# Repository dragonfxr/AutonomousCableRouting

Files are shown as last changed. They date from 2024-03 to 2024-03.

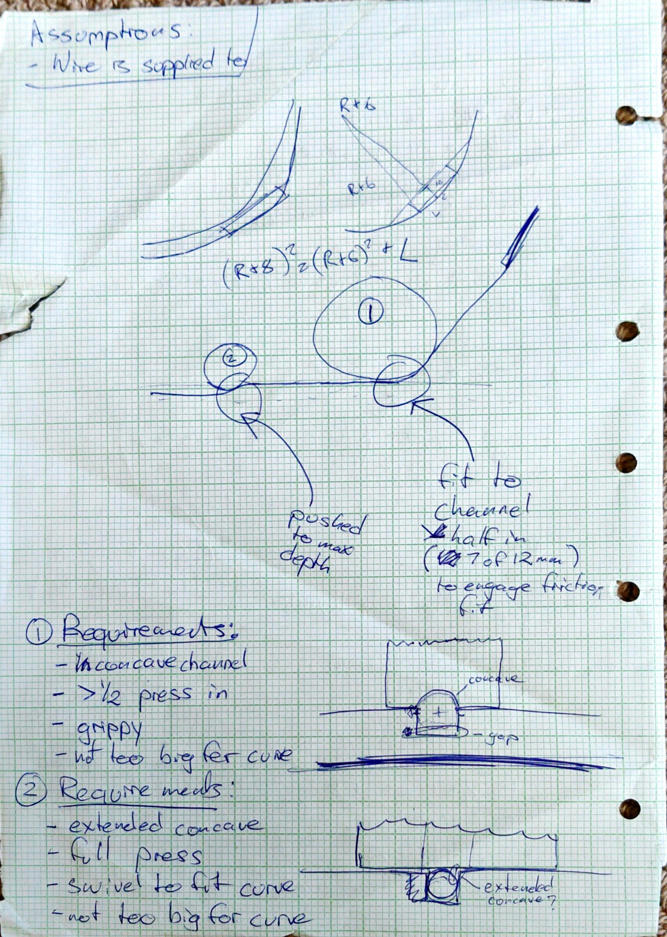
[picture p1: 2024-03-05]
Compendium/4. Routing/Design Evolution/General Sketches/2021_10_18 2_13 PM Office Lens.jpg

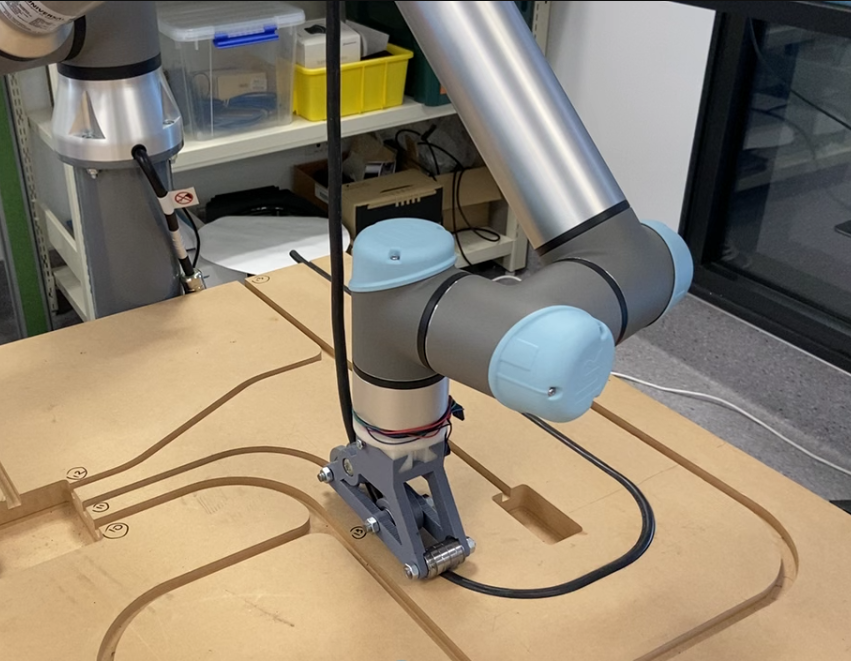
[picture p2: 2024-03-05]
Compendium/4. Routing/Final Design/Photos and Videos/process3.png

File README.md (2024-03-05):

# AutonomousCableRouting
https://www.youtube.com/watch?v=44ud-408be0

## Project Title
Research project on Autonomous Routing and Connection of Multi-Core Cables into Prefabricated Walls.

## Project Description
The demand for affordable housing is increasing rapidly. Driven by high labour costs, home
prices are climbing ever higher. Therefore, some new methods are introduced to reduce
construction costs. A solution is the automatic pre-fabrication of homes, improving construction
efficiency in terms of time and labour cost. This project focuses on automating the handling
and routing of electrical cables in pre-fabricated walls, employing a sophisticated robotic
end-effector, a path planning scheme to appropriately control the robot arm, and specially
designed connector solutions for connecting individual cable cores in 3-way junctions.

The proposed robotic end-effector is equipped with a cable feeding mechanism and it
can press-fit the electrical cables into narrow channels created in concrete pre-fabricated
walls. The end-effector shows reliable and repeatable operation. The research also presents
two types of connector designs that can facilitate the connection of the cable cores in the
junctions of pre-fabricated walls. The installation of connectors is based on a machine
vision framework implemented in MATLAB. The machine vision framework can identify
the colours of cables and locate the cables.

Robot programming and path planning relied on kinaesthetic teaching. The results showed
the speed of routing using robotic arms far exceeds manual routing.

## Acknowledgement
I would like to thank the following:

Zach Macleod, my project partner, for his passion for the project, excellent critical thinking
and professional engineering skills.

Dr Minas Liarokapis, our project supervisor, for the time and guidance throughout the
project and many suggestions are given to us.

Zuru Tech for their opinions on the project.

# How to have a look
You can always click and check the files above. If they are not obvious, please try the following:

## Video on Youtube
https://www.youtube.com/watch?v=44ud-408be0&list=PLSRmLAcBxallVHnpcKzguajrszkn9cb2G&index=4&t=2s

## Link for the research report
[Report.pdf](https://github.com/dragonfxr/AutonomousCableRouting/files/14495556/Report_xfen422.pdf)

# How to contact
If you have more advice on the project or you want to me some hints, please contact me.

Email:

russell.feng.au@gmail.com

I'm always open to feedback and collaboration. Looking forward to hearing and learning from you!

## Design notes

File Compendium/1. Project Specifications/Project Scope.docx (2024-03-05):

# Project Scope

# Research Objectives

To produce an acceptable solution for the required system, the following objectives need to be met:

- Identify what processes must be performed on an electrical cable before routing.
- Investigate what perception methods are needed to identify and localise flexible cables.
- Investigate what methods should be employed to facilitate the efficient execution of cable handling and manipulation tasks.
- Investigate what design characteristics are needed for the development of an end-effector that can manipulate flexible cables effectively.
- Examine possible cable grasping mechanisms and techniques and their capability tovary grip strength and agility.
- Examine suitable connection methods of multi-core electrical cables at 3 way junc-tions.
- Investigate what design characteristics are needed for the development of an end-effector that can install electrical connections effectively.
- Identify what methods are required to implement a routing system fully autonom-ously and ensure errors are handled correctly.
- Analyse the return on investment of the routing system compared to manual labour

# Exclusions

The following are excluded from the scope:

- Structural analysis and strengthening of parts for long life in industrial context.
  - This is because the conditions of future use are not clear, so instead the designs are used as proof of concept.
- Robot arm path planning.
  - This is because ZURU Tech has extensive knowledge and capability for path planning, further consideration would be trivial.
- Stepper motor speed control.
  - This is because motor control is already a very well-defined process, further consideration would be trivial.

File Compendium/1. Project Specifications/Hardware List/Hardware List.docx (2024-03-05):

# Hardware List

Following are the names and brief descriptions of the hardware used throughout the project:

- Prusa 3D Printers
  - A variety of Prusa 3D printer models were available for use. Used for rapid prototyping of routing end-effector models.
  - Available in the 3D printing and mechatronics labs in the 405 building at the University of Auckland. Requires training.
- Universal Robots UR5e Robot Arm
  - A mid-size robot arm which is simple to program. Used for initial testing of routing end-effector prototypes.
  - Available in the robot cell in the mechatronics lab in the 405 building at University of Auckland. Requires training.
  - Manual included.
- KUKA KR16 Robot Arm
  - A mid to large size robot arm which will be used in real-world application. Not used in this project.
  - Available in the robot cell in the mechatronics lab in the 405 building at University of Auckland. Requires training.
  - Technical specs included.
  - Serial number: 859871.
- NEMA17 Stepper Motor
  - A stepper motor for accurate and precise motor control. Used for feeding a cable for routing.
  - Available at request from technicians in the mechatronics lab in the 405 building at University of Auckland.
  - Technical specs included.
- DRV8825 Stepper Motor Driver
  - A motor driver for interfacing stepper motors to control circuits. Used for driving the NEMA17 stepper motor.
  - Available at request from technicians in the mechatronics lab in the 405 building at University of Auckland.
  - Technical specs included.
- Arduino Uno Rev3
  - A microcontroller to control stepper motor function. Used for controlling the NEMA17 stepper motor.
  - Available at request from technicians in the mechatronics lab in the 405 building at University of Auckland.
  - Schematic included.
- KINGSING KS-W1022 Multi-Core Cable and Stripping Machine
  - A stripping machine which can cut cables to length, automatically strip outer sheaths and core insulations. Used for stripping and cutting multi-core cable to the desired lengths for routing.
  - Bought by ZURU Tech for project use.
  - Manual Included.
- Sample Wall
  - A sample wall fabricated from MDF for testing of routing function.
  - Available in the mechatronics lab in the 405 building at University of Auckland or for request by engineering workshop technicians.
- Multi-Core Cables
  - Electrical cables to be routed into channels. Variety of 3-solid-core power cables and 4-stranded-core data cables.
  - Purchased by the technicians of the mechatronics lab in the 405 building at University of Auckland.
  - Specification in directory “\3. Cable Stripping Methods\Criteria”
- Consumables (by use)
  - Stepper motor circuit
    - Breadboard
    - Jumper wires
    - Capacitor
  - Routing end-effector prototypes
    - Threaded rods
    - Bolts
    - Machine screws
    - Socket screws
    - Nuts
    - Threaded inserts
    - Ball bearings
    - PLA filament
    - Elastic bands
- Workshop Tools
  - Soldering iron station
  - DC Power source
  - Multimeter
  - Manual wire stripper
  - Side cutters
  - Drill
  - Mallet
  - Hacksaw
  - Files
  - Screwdrivers
  - Allen keys
  - Spenners
  - Pliers
  - Vernier caliper
  - Utility knife
  - Scraper
  - PPE

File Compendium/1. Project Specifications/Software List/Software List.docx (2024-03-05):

# Software List

Following are the names and brief descriptions of the software used throughout the project:

- Google Drive
  - The shared file storage system was essential for accessibility and collaboration. Functionality for document creation was also used for presentation preparation, note taking and brainstorming.
  - Free online service - accessed through university Google accounts.
- Microsoft Office Suite
  - The Word and Powerpoint applications were useful for report writing and slideshow presentations respectively. They generally create a slightly more refined finish than Google Drive.
  - Licensed through the University of Auckland - free for students.
- Overleaf
  - Useful tool for creating an organised and polished final report. Outputs a professional looking document.
  - Licensed online software through the University of Auckland - free for students.
- Autodesk Inventor Professional 2019/2021
  - 3D CAD modelling software for creating designs, printable parts and renders.
  - Licensed through the University of Auckland - free for students.
- PrusaSlicer
  - Open-source slicing software for generating a 3D printable G-code file from a stl CAD file. Designed specifically for Prusa 3D printers which are used heavily by the University of Auckland.
  - Free through the University of Auckland - free for students.
- MATLAB
  - Versatile high-level programming language. Used for function calculations and image processing scripts.
  - Licensed through the University of Auckland - free for students.
- Arduino IDE
  - Open-source programming software designed to be compatible with an Arduino microcontroller. Used for stepper motor control.
  - Free downloadable software.
- Fritzing
  - Electronics circuit and PCB design software. Used for design of stepper motor control circuit.
  - Paid downloadable software.
- UR5e Robot Arm Controller
  - Built-in controller software for programming movement of a UR5e robot arm. Used for testing of routing end-effectors by moving by a manually defined path.
  - Available for use at the University of Auckland
  - Manual included in directory “\1. Project Specifications\Hardware List”

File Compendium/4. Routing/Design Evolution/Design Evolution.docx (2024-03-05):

# Design Evolution

# Prototype 1: Hand-held Roller

Designed as an initial test for rolling a cable into the sample wall. Was designed to be spring loaded and hand-held. For 10mm stranded cable. CAD models were deleted.

Design was abandoned in favour of a robot-mounted one.

## Advantages:

- Concave wheel profile

## Issues:

- Requires large downwards force
- Requires many elastic bands
- Prone to slipping
- Difficulty with corners

# Prototype 2: Crank Feeder

Designed for no contact to the sample wall, just to feed the cable with enough force to press-fit. Hand-cranked for 10mm stranded cable. CAD models were deleted.

Design was abandoned.

## Advantages:

- Concave wheel profile
- No contact/wear with wall

## Issues:

- Requires large grip force
- Prone to slipping
- Push-fit depth is unpredictable
- Prone to cable raising after routing
- Design tolerances were too big
- Hand cranked

# Prototype 3: Framed Roller Initial

Designed for robust routing and lowered variability. A series of wheels would align then press the cable into the channel. For 12mm solid cable.

## Advantages:

- Concave wheel profile
- Robust routing method

## Issues:

- Hole-edge distance too small
- Structure is too thin and flimsy
- Not enough holes for arm mounting
- Feeding hole didn’t work
- No stepper

# Prototype 4: Framed Roller Iteration 1

Iteration of previous prototype. For 12mm solid cable. Some CAD files altered and no renders.

## Advantages:

- Concave wheel profile
- Robust routing method
- Increased thickness of structure (including hole-edge distance)
- Better arm mounting holes
- Replaced feeding hole with roller

## Issues:

- No Stepper
- Arm mounting holes don’t fit screws

# Prototype 5: Framed Roller Iteration 2

Iteration of previous prototype. For 10mm stranded cable for better performance. All CAD files altered and no renders.

## Advantages:

- Concave wheel profile
- Robust routing method
- Increased thickness of structure (including hole-edge distance)
- Replaced feeding roller with a stepper motor driven feeding mechanism

## Issues:

- Loaded feed wheel doesn’t close enough
- Stepper mount screws stick out too much
- Stepper mount screws are incorrectly positioned
- Arm mounting holes don’t fit screws
- Driven wheel isn’t supported opposite stepper properly - screw doesn’t thread into anything
- Feed wheels sometime slip

# Prototype 6: Framed Roller Final Iteration

Iteration of previous prototype. For 10mm stranded cable.

## Advantages:

- Concave wheel profile
- Robust routing method
- Increased thickness of structure (including hole-edge distance)
- Replaced feeding roller with a stepper motor driven feeding mechanism
- Increased movement on loaded wheel
- Bored and rearranged stepper mount screws
- Changed arm mounting to dovetail mount with extra piece
- Inserted screw “key” opposite stepper on driven wheel

## Issues:

- Feed wheels sometime slip
- Does not accommodate different cable sizes
- Stepper motor struggles (might just be making lots of noise)

# General Sketches

Workbook sketches which detail previous designs and iterations.

# Stepper Motor

Contains:

- Fritzing circuit diagram for the stepper motor
- Figure of circuit diagram
- Basic stepper motor control script
- Stepper motor circuit description

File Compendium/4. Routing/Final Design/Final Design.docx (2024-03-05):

# Final Design

# Description

Read the end of year reports in “\9. Deliverables” to read a description of the final end-effector design.

# Process

- A cable to be routed is gripped between the driven and loaded wheels as the spin.
- The cable is then fed to the aligning wheel which will place the cable into the channel and half press-fit it.
- The push roller will then roll over the half pressed cable and fully press-fit it into the channel.

# Connection to Robot Arm

A dovetail shaped mount is bolted onto either the KR16 or UR5e robot arm. Then the frame of the end-effector is slid on the dovetail and bolted with a through-hole.

# Issues:

- Feed wheels sometime slip
- Does not accommodate different cable sizes
- Stepper motor struggles (might just be making lots of noise)

# Results:

Successfully routed 11 out of 12 initial runs with a 10mm stranded core cable. The failure mode was only slight lifting of the cable, but not removal from the channel.

Routes path in 16s.

Can also route 12mm solid core cables, however, no records were taken from this.

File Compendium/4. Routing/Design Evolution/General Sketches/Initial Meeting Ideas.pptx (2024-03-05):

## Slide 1

Russell and Zach
Conceptual designs combined together to create a working whole - or separated for use in different solution

Potential solution for groove-alignment, adhesive-
extrusion & rolling-cable-layer

Side view:

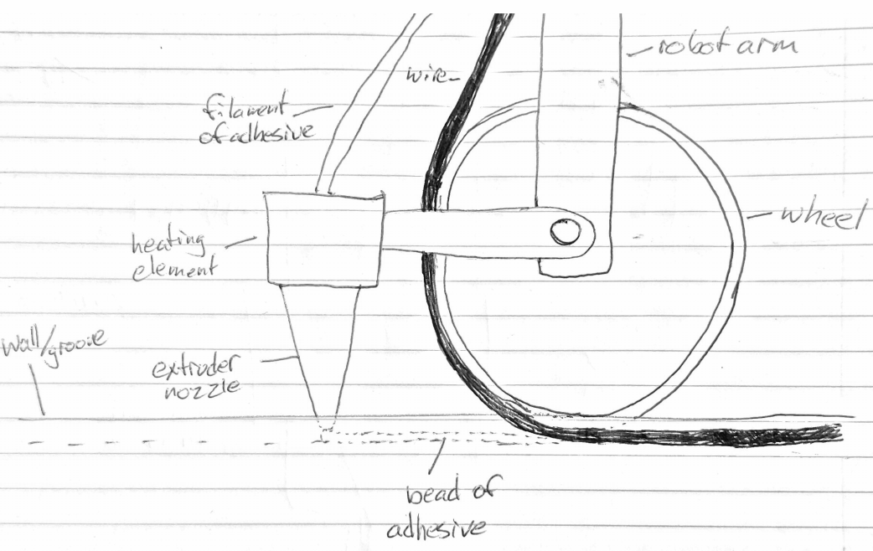
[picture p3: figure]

Potential Process:
Use a separator to separate each core by wire stripping with a moveable blade

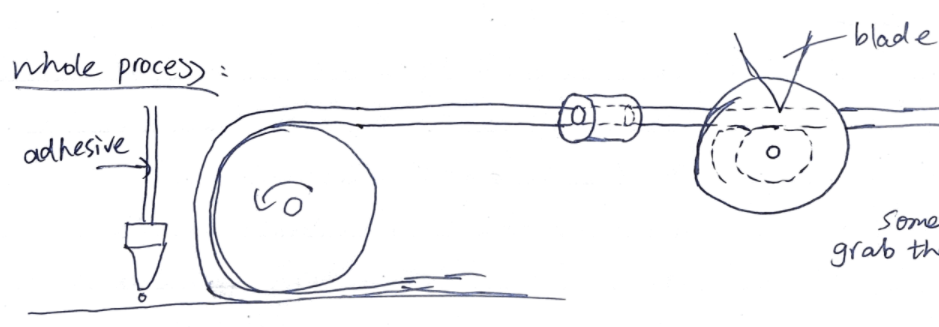
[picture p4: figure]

Potential Process: Repeated use of static mounted wire-stripping tool

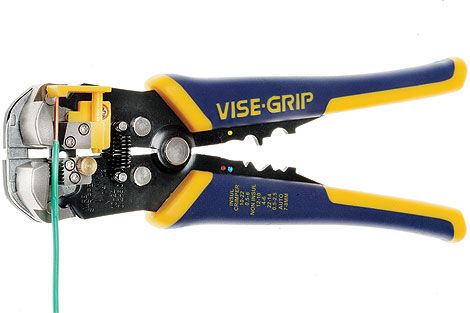
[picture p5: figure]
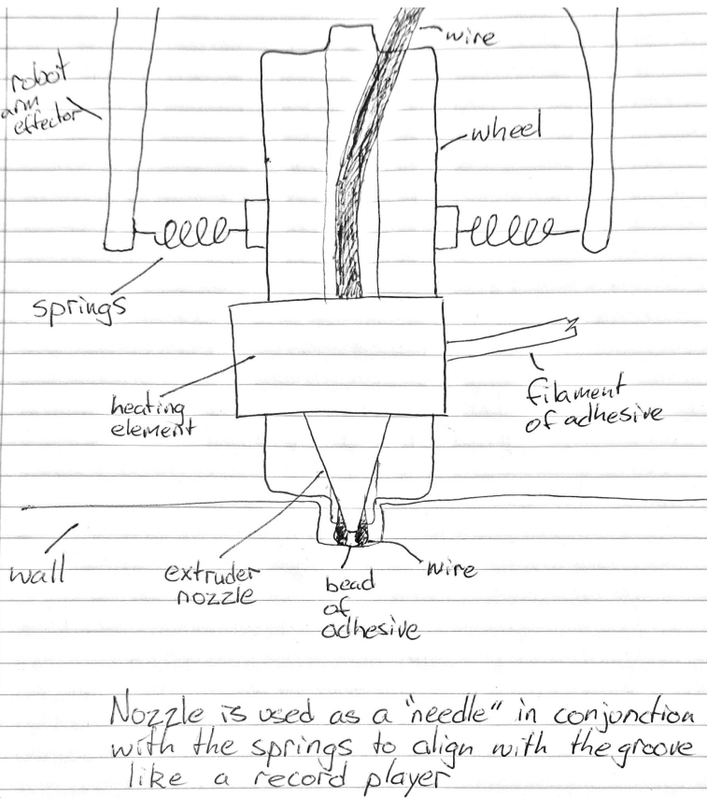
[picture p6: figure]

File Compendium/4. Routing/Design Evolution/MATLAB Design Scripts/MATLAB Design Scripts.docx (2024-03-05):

# MATLAB Design Scripts

1. MaxAlignWheelRadius

Finds the max radius of the drive wheel considering the radius of the cable to be layed, the min depth that the cable is to be pushed in (from middle of the cable) and the min ratio of the total cable press force which is pushing the cable down.

Discarded from prototype 4 because the aligning wheel no longer fits into the channel.

2. PushRollerBearingCount

Finds the number of bearings needed for the push roller considering the radius of the cable to be layed, the horizontal distance between the two axles, and the width of the bearings.

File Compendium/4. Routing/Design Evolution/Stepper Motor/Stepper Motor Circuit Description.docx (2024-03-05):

# Stepper Motor Circuit Description

The stepper motor circuit contains:

- NEMA17 stepper motor
- Jumper wires
- Basic breadboard
- 100 microfarad capacitor - for reducing voltage spikes on connection
- DRV8825 stepper driver
- Arduino Uno Rev3 microcontroller
- Power source - found to work well at 20V

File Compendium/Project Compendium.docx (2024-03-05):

Compendium Structure

The project compendium provides all materials needed for the project

1. Project Specifications
- Zuru Tech Materials
- Hardware List
- Software List
- Project Scope
2. Related work
3. Cable Stripping Method
4. Routing
- Final Design
- Design Evolution
5. Connector
- Insulation Piercing Connectors
- Insulation Displacement Connectors
- Initial Sketches
6. Image Processing
- MATLAB Script and Sample Images
- Indicative Progress Images
7. Future Work
8. Meeting Minutes and Slides

What is in each folder:

Project Specifications

The hardware and software required for the project, including manual and specification sheets for equipment.

Related work

The existing research related to the project. All research documents are categorized according to topics.

Cable Stripping Method

The cable stripping method selection criteria and video and photo of the selected stripping machine.

Routing

This folder contains the design evolution of the end-effector, including four prototypes, MATLAB scripts used in design and the stepper motor design. The CAD model, videos and photos for the final design is also in this folder, including the routing process and cable feeding using stepper motor.

Connectors

The CAD models and renders of two types of connectors as well as the initial brainstorming sketches.

Image Processing

This folder contains the MATLAB script used for image processing, sample Images and indicative progress images.

Future Work

A document describes the potential further development.

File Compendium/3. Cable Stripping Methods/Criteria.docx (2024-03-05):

# Criteria

# Cable Specifications

All cores are covered in coloured PVC insulation and a separate black outer PVC sheath.

Identification No. | No. of Cores | Cross-Sectional Area (mm²) | Core Type | Usage
1 | 3 | 2.5 | Solid | Power
2 | 3 | 4 | Solid | Power
3 | 3 | 6 | Solid | Power
4 | 4 | 1.5 | Stranded | Data
5 | 4 | 2.5 | Stranded | Data

# Cable Stripping Methods Comparison

Stripping Method | Advantages | Disadvantages
Laser | - Fast - Experiences no wear - Insulation vaporised | - Manual removal is required - Expensive
Chemical | - Cheap | - Not fit for purpose (magnet wires only) - Slow - Not environmentally friendly
Mechanical (chosen) | - Suitable for multi-core cable cutting. - Automatic removal | - Need to purchase from China
Abrasive | - Fast | - Leftover insulation dust - single-core cables only

# Alternative Methods

The following stripping methods were excluded from comparison because they were clearly not fit for purpose:

- Ultrasonic
  - Very uncommon
- None
  - Infeasible for accurate connection

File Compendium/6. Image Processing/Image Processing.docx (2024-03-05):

# Image Processing

The image processing takes images of the cables after they have been routed. Then the MATLAB script is given images which are cropped from the taken photo. The script gives the order of insulation colours of the cores so that they can be correctly connected.

For more information on the MATLAB script, read the description in the file. For more information on the process, read the final reports in “\9. Deliverables".

# Assumptions

- Unchanging light and camera conditions so that colours are not subject to much variation in images.
  - Achieved by mounting an LED on the connector end-effector.
- The images can be taken from the same place relative to the junction each time so that the script knows where to identify the insulation could patterns every time.
  - Achieved by mounting the camera on the connector end-effector and path planning for this process.

# Indicative Process Images

1. Shows the working line of the script.
2. Shows only the pixels identified as one of the insulation colours, as well as the working line.
3. Shows the average rows for each insulation colour, as well as the workling line.

# Results

100% accuracy with the sample images. The differing light conditions require the range of brown to be altered.

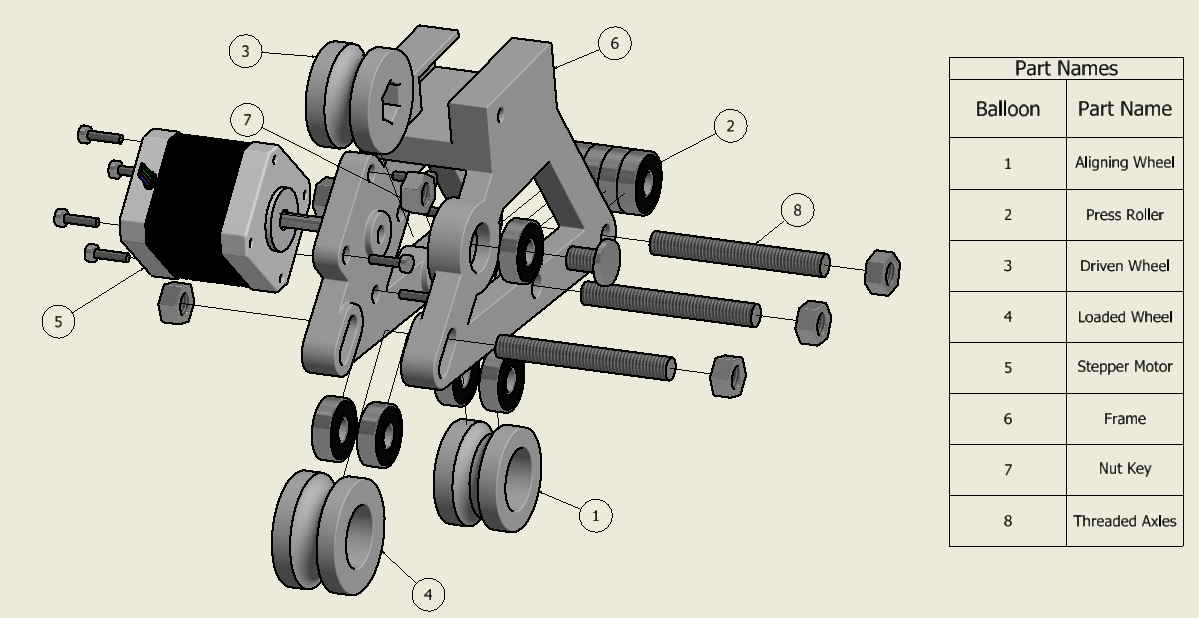
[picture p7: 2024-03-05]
Compendium/4. Routing/Final Design/CAD and Renders/Exploded.PNG

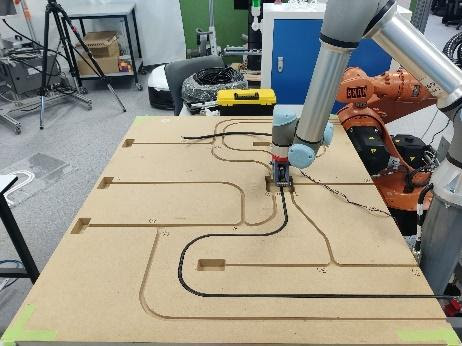
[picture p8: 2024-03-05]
Compendium/4. Routing/Final Design/Photos and Videos/timeseries6.jpg

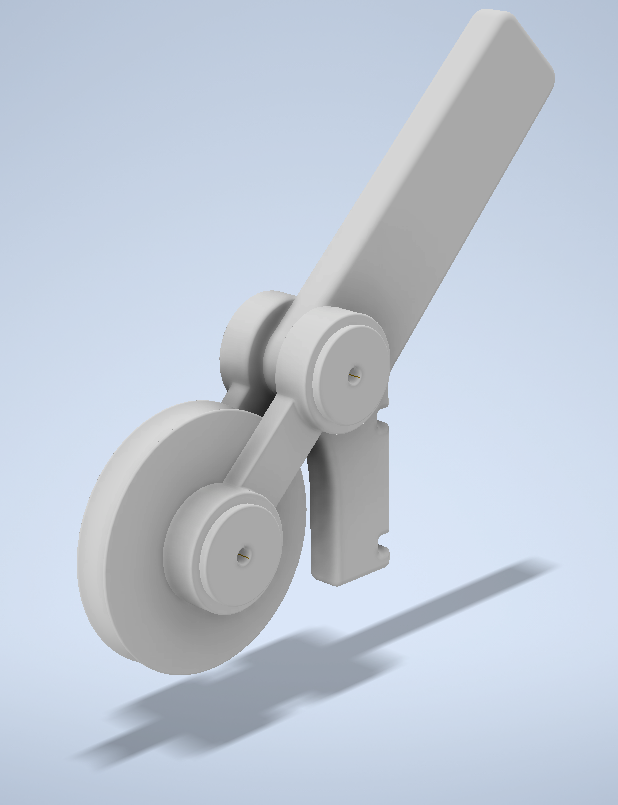
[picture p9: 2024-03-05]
Compendium/4. Routing/Design Evolution/Prototype 1_ Hand-held Roller/Prototype 1 Render.PNG

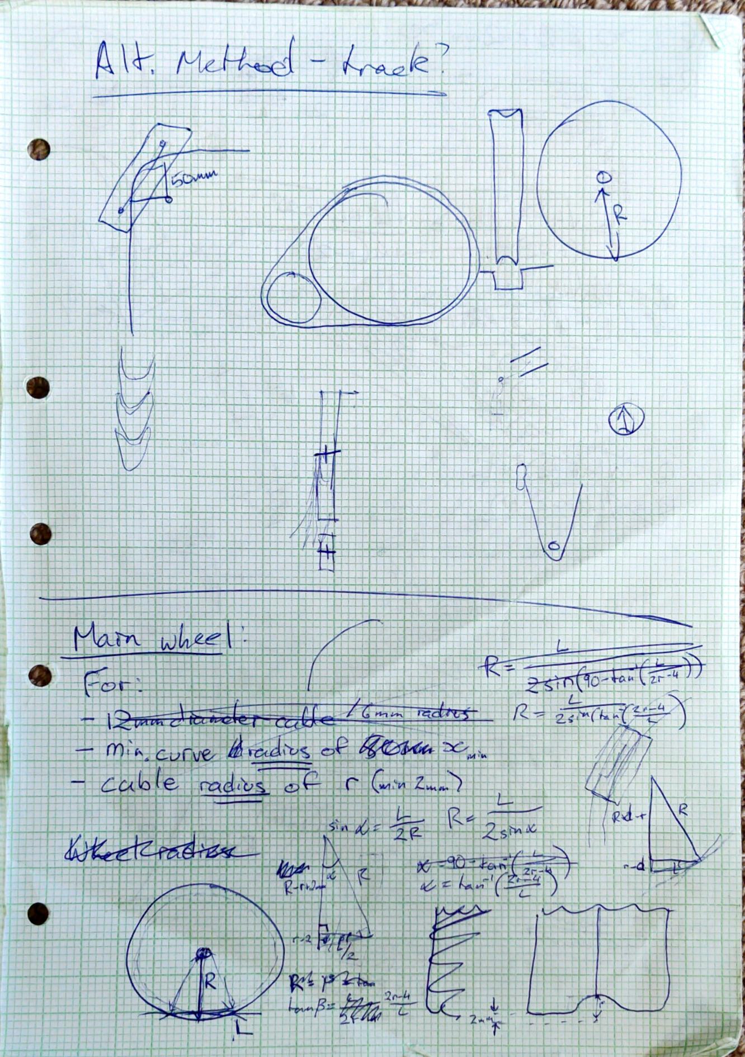
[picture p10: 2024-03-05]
Compendium/4. Routing/Design Evolution/General Sketches/2021_10_18 2_14 PM Office Lens.jpg

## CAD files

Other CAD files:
Compendium/4. Routing/Final Design/CAD and Renders/Assembly.dwg
Compendium/4. Routing/Design Evolution/Prototype 3_ Framed Roller Initial/KukaHead.0012.ipt
Compendium/4. Routing/Design Evolution/Prototype 4_ Framed Roller Iteration 1/AlignWheelHalf_12mm.ipt
Compendium/4. Routing/Design Evolution/Prototype 4_ Framed Roller Iteration 1/Assembly_NoStepper.iam
Compendium/4. Routing/Design Evolution/Prototype 4_ Framed Roller Iteration 1/Frame_12mm_nostepper.ipt
Compendium/4. Routing/Design Evolution/Prototype 4_ Framed Roller Iteration 1/LeadWheel_12mm.ipt
Compendium/4. Routing/Final Design/CAD and Renders/AlignWheelHalf_10mm.ipt
Compendium/4. Routing/Final Design/CAD and Renders/Assembly.iam
Compendium/4. Routing/Final Design/CAD and Renders/Assembly.ipn
Compendium/4. Routing/Final Design/CAD and Renders/Bearing.ipt
Compendium/4. Routing/Final Design/CAD and Renders/DriveWheel_10mm.ipt
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

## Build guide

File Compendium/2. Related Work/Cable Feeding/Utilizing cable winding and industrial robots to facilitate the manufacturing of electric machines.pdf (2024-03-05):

## Utilizing cable winding and industrial robots to facilitate the manufacturing of electric machines

## Erik Hultman n , Mats Leijon

Division for Electricity, Uppsala University, Box 534, 751 21 Uppsala, Sweden

article info

Article history:
Received 18 November 2011
Received in revised form
5 June 2012
Accepted 25 June 2012
Available online 24 July 2012

Keywords:
Stator winding
Automated production
Industrial robot
Electric machine assembly
Powerformer
Wave energy converter

abstract

Cable wound electric machines are used mainly for high voltage and direct-drive applications. They can be found in areas such as wind power, hydropower, wave power and high-voltage motors. Compared to conventional winding techniques, cable winding includes fewer manufacturing steps and is therefore likely to be better suited for automated production. Automation of the cable winding production step is a crucial task in order to lower the manufacturing costs of these machines. This article presents a production method using industrial robots for automation of cable winding of electric machine stators. The concept presented is validated through computer simulations and full-scale winding experiments, including a constructed robot-held cable feeder tool prototype. A cable wound linear stator section of an Uppsala University Wave Energy Converter and its winding process is used as a reference in this article. From this example, it is shown that considerable production cycle time and manufacturing cost savings can be anticipated compared to manual winding. The suggested automation method is very flexible. It can be used for the production of cable wound stators with different shapes and sizes, for different cable dimensions and with different winding patterns.
& 2012 Elsevier Ltd.
1. Introduction

Fully automated manufacturing of conventional electric machines, both motors and generators, is well known today and has been globally introduced in factories for a few decades [1–5]. It has been widely recognized that automated production lines are necessary to survive in today’s global electric machine market [6–8]. Designing with production in mind has been an important key in the process towards automation of electric machine manufacturing [2,5,9].
One of the most challenging operations to automate in electric machine manufacturing is the winding of the stator. For conventional machines using coils of inductor wire or rectangular inductor bars, different automated winding methods have been developed. A less common electric generator design, known as the Powerformer, utilizes cables for the stator winding. This concept has some important advantages, including reduced system losses and fewer winding production steps [10–15]. However, no published fully developed automated cable winding production method has been found.
Advances in the industrial robot technology during the last years have enabled robotized automation of advanced tasks that could only be done manually before, some with similarities to winding technology. They also allowed increased production volumes and flexibility for already existing automated production lines [16–22]. A driving actor in this is the automobile industry, with large investments in fully robotized automated production lines along with research and development of new robot applications for manufacturing [23–25]. Industrial robots often introduce more flexible automation solutions, due to their large workspace and programming possibilities, compared to methods based on task-specific, stiff automation machines. This flexibility is very suitable for the production of electric machines since rapid changes in production due to small and often varying product series are common. Thus robots are sometimes used for stator winding operations [7,26].
A specific cable winding process, the stator winding of a direct-driven linear permanent magnet cable wound generator stator section used in an UU WEC,¹ will be used in this article to exemplify a full-scale cable winding production step.
The aim of the work presented in this article is to suggest and validate a production method to facilitate electric machine manufacturing by using industrial robots to automate cable winding in electric machine stators. Even though the generator example presented here is a linear generator used in a WEC, the presented method should be applicable for other cable wound electric machines as well, including the more common rotating machines.

Contents lists available at SciVerse ScienceDirect

journal homepage: www.elsevier.com/locate/rcim

# Robotics and Computer-Integrated Manufacturing

0736-5845 & 2012 Elsevier Ltd.
http://dx.doi.org/10.1016/j.rcim.2012.06.005

n Corresponding author. Tel.: þ46 18 471 34 96; fax: þ46 18 471 58 10.
E-mail address: erik.hultman@angstrom.uu.se (E. Hultman). | 1 Uppsala University Wave Energy Converter.

Robotics and Computer-Integrated Manufacturing 29 (2013) 246–256

Open access under CC BY-NC-ND license. (http://creativecommons.org/licenses/by-nc-nd/3.0/)

Open access under CC BY-NC-ND license. (http://creativecommons.org/licenses/by-nc-nd/3.0/)

2. Method

The development of an industrial robot production cell is a complex task with many different steps. Some key methods used in this work have been: the choice of an appropriate robot model, the design of equipment in a 3D-CAD environment, offline robot cell programming and experiments, the construction of a cable feeder tool prototype and full-scale winding experiments. The main process chain is explained in Fig. 1.
Since this is an iterative process where the cell and tool design, robot programming and winding process are adjusted to each other numerous times before a satisfying solution is found, the results in Sections 4–6 only present the final versions of the automation method, the robot cell layout, the cable feeder design and the robot cell simulations.
2.1. Computer simulations of the robot cell

Offline robot programming can be an important key in evaluating and designing a new robot cell, before building a full scale cell. In this paper, ABB RobotStudio [27] is used for offline robot simulations. With this computer software, appropriate industrial robot models and number of robots regarding reach and positioning can be investigated. Also, the reach of the robots over the work object can be optimized with different tool designs. As the robot models, tool design and cell design are decided, the full robot programming can be tested with the simulation cell, including simulating sensors. However, even though offline software can save expensive robot and production time, some special events and physical states, including deformable objects, might be hard to fully simulate. Thus offline simulations must often be followed by full scale physical robot cell experiments.

2.2. Economical calculations

A new automated robot cell should be economically evaluated and compared to present and alternative production methods. One important figure, used to determine the value of the investment, is the net present value, which is calculated using Eq. (1) where NPV is the net present value, n is the economical lifetime of the investment, Ct is the net cash flow at time t and i is the discount rate. Another useful figure is the payback period, which is calculated by solving Eq. (2) where T is the payback period. NPV ¼ Xn

t ¼ 0

Ct
ð1þiÞ
t | ð1Þ

XT

t ¼ 0

Ct ¼ 0 | ð2Þ
3. Automated cable winding

This section presents some necessary background theory in developing an automated cable winding production cell, including existing stator winding techniques, the Powerformer concept, the WEC stator winding example used in this work, the most important design requirements and the basic conceptual choices used as a starting point for this automation.

3.1. Stator winding schemes

An electric machine can either be a motor, converting electric energy to mechanical energy, or a generator, converting mechanical energy to electric energy. The two main parts of an electric machine are a rotating rotor and a stationary stator. For linear machines, a linearly moving translator replaces the rotor. The basic process of the electromechanical energy conversion can be demonstrated by moving a magnet in and out of a closed conductor loop. The mechanical energy moving the magnet converts to electric energy, inducing a voltage and a current starts to flow in the conductor. This represents a linear generator design where the magnet illustrates the translator part and the conductor loop illustrates the stator. In an electrical machine the conductor loop is usually mounted inside slots in the stator and is referred to as the stator winding.
The ratio of the in-slot winding cross section area to the total available slot area, referred to as the slot fill-factor, is often used to describe stator windings. For a given stator design, the slot fill-factor represents the level of material utilization in the machine and therefore it is desired to have this ratio as high as possible. However, the slot fill-factor cannot be used by itself when comparing different stator designs since other aspects often influence the overall machine performance more.
Conventional electric machines mainly use strands of inductor wire or rectangular inductor bars for the stator winding, see Figs. 2 and 3. Using the inductor wire strand design, the coils can either be wound directly in the stator slots using special tools or be prepared outside the stator and then inserted into the stator slots. In-slot winding eliminates the extra production step of inserting the coils into the stator. On the other hand this method is not able to create windings with as high a slot fill-factor as outside winding, since the winding tool requires some space inside the slot and there is a minimum distance required between the stator teeth in order for the winding tool to be able to reach inside the slots [28].

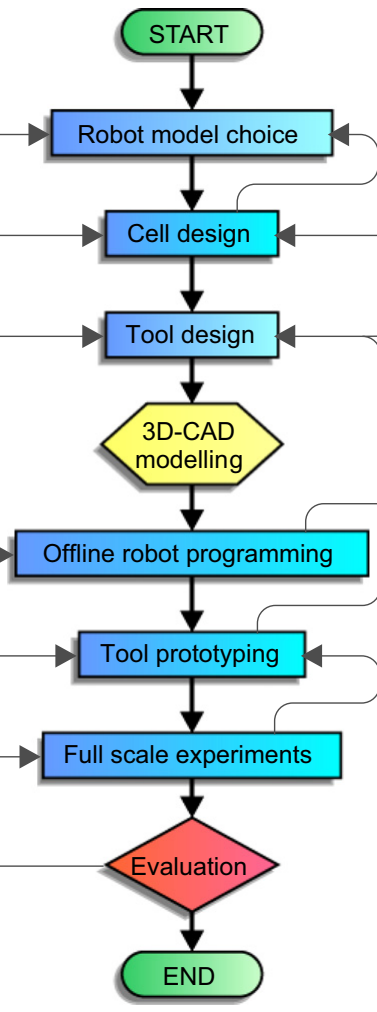
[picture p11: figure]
START; Robot model choice; Cell design; Tool design; 3D-CAD modelling; Offline robot programming; Tool prototyping; Full scale experiments; Evaluation; END

Fig. 1. Method used in the work described in this article.

E. Hultman, M. Leijon / Robotics and Computer-Integrated Manufacturing 29 (2013) 246–256 | 247

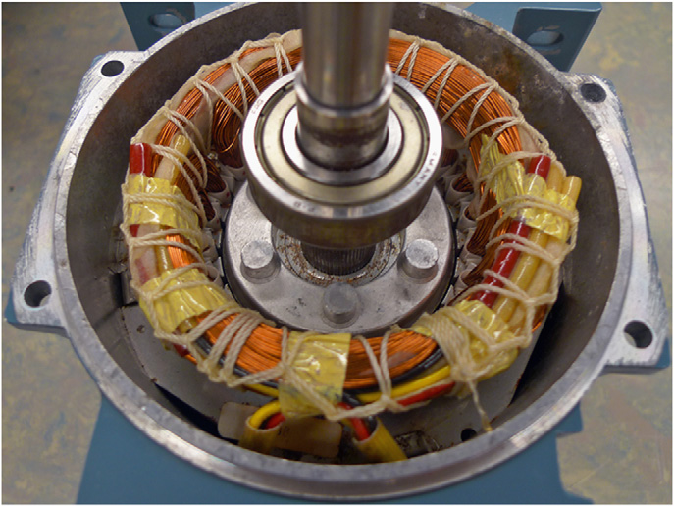
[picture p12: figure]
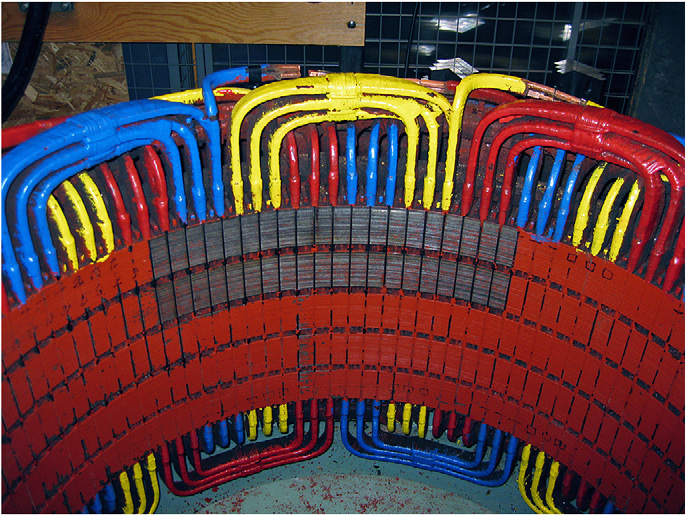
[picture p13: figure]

Preparing the windings outside the stator enables better packed and larger windings with a higher slot fill-factor, but the windings must be inserted into the slots and the stator design must be adjusted for this [9]. An alternative method is to split the stator in toothsegments and wind each segment separately [29–32]. As a result, a higher slot fill-factor can be accomplished, but an extra assembly production step for the stator is introduced. Other research suggests a sectional stator design that allows the stator slots to be opened to facilitate the winding and improve the slot fill-factor [33]. When it comes to larger machines, mostly generators, rectangular inductor bars are often used for the stator winding. Automation for insulating and forming these bars is available but the insertion is mostly done by hand due to the small production series and the large generator size [3]. Automated winding techniques for other generator designs exist too [34]. Insulation of the windings, winding fixation and end windings connection are important production steps for all conventional electric machine stators.

3.2. Cable wound machines

Cable wound generators, a concept known as the Powerformer or Very High Voltage machines, have some important advantages compared to conventional generators. Using high voltage power cables in the stator winding, a Powerformer generator allows generation of electricity at grid transmission voltage levels, thus eliminating the need for a step-up transformer between the generator and the grid. Among the benefits with this technique are reduced system losses, better network stability, smaller investment costs and less overall environmental impact [10–15]. Another important advantage of cable wound electric machine stators is that the number of manufacturing assembly steps for the stator winding are reduced. Using power cables in the winding eliminates the production steps of insulating the windings during the stator assembling, possible insertion of pre-wound coils into the stator slots and securing the windings in the stator slots, while the need for end windings connection is reduced. The full cable winding process is performed by feeding the power cables back and forth through the stator slots, from the top and bottom of the stator. Since cable wound generators and motors are still much less common than their competitors and because only small series with large machines based on this technique have been manufactured today, there is as yet no method developed for fully automated cable winding of electric machines. Manually assisted cable winding of large-scale generators are these days performed with the help of several cable feeder tools [35].

3.3. The UU WEC stator cable winding example

The specific cable winding example considered in this article is the stator winding of a direct-driven linear cable wound generator used in a WEC unit prototype constructed within the Lysekil project at The Swedish Centre for Renewable Electric Energy Conversion at Uppsala University. This technology is described in more detail in [36,37]. Fig. 4 shows the UU WEC generator design, Fig. 5 shows a cable wound UU WEC stator section that is mounted inside an UU WEC. The stator section is about 2 m long, about 0.5 m wide and is divided in the middle by a 30¹ angle. The slot hole diameter, through which the winding cable is fed, is 8 mm and the average outer diameter of the winding cable is 7.2 mm. A three-phase wave winding pattern with some modifications is used. This article will however assume and focus on a pure three-phase wave winding, see Fig. 6, since this is an obvious starting point even for other winding patterns.
A condition for this WEC technique to be competitive on a global market is that the production cost is low. The technique is intended for future large series production, which makes the manufacturing suitable for automation. Automated cable winding has an important role in this process.

Fig. 3. A stator winding with copper bars, in a hydropower generator.

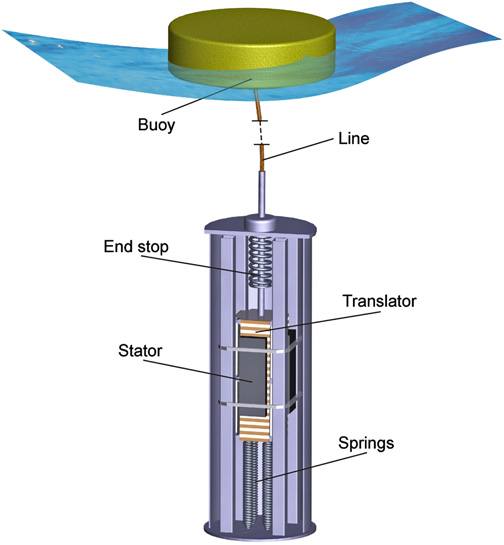
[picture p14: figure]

Fig. 4. The UU WEC unit design.

Fig. 2. A stator winding with strands of induction wire, in a small electric motor.

248 | E. Hultman, M. Leijon / Robotics and Computer-Integrated Manufacturing 29 (2013) 246–256

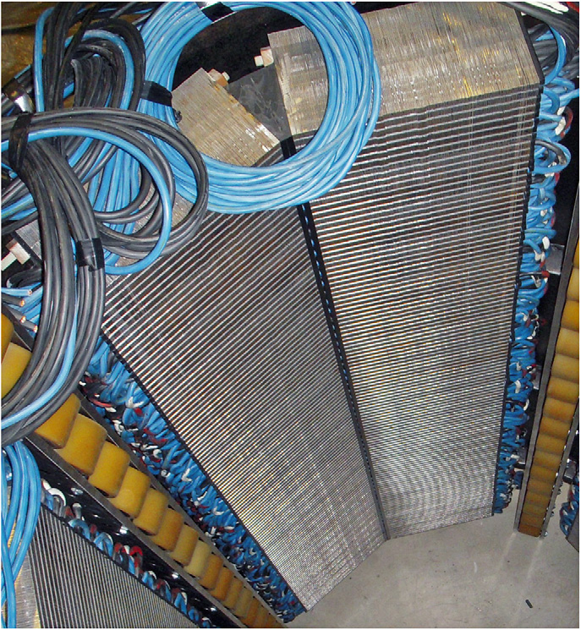
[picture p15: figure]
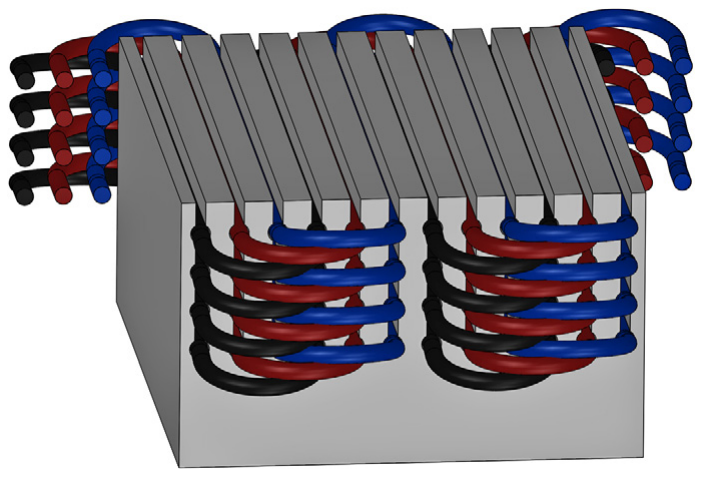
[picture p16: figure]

3.4. Requirements of automated cable winding

In developing an automation method for cable winding, some important general cable winding issues, presented in this subsection, must be considered.
As can be understood from the UU WEC stator example in Figs. 5 and 6, a cable must be fed from the sides of the stator slot by slot, so insertion of a complete winding from above is not possible. Numerous cables are instead fed back and forth through the whole stator in a specific winding pattern. The cables are then connected to each other at the end of the windings. A high stator slot fill-factor is desired; therefore the cables must be fitted tightly into the slots. The cable must be handled with care to avoid being damaged due to for example a too small bending radius, buckling or wear. Enough high cable feeding forces must be guaranteed so that the cable does not get stuck inside the stator during winding. The fed length of the cable must be controlled in order to get short end windings on the stator sides. During the winding process, earlier created end windings must sometimes be pushed down to prevent them from covering unwound slot holes and disturb the winding process. Some further general requirements of the automation are that the layout of the automation should be suitable for direct implementation in a factory production line, the need for human interaction in the production is kept to a minimum and the automation method is as simple and robust as possible. Moreover, high flexibility is needed to enable adjustments to production of different machines and the winding production cycle time and investment cost must be low.
Regarding flexibility, there are a few aspects to keep in mind. To begin with, it is important that the final automation method can be adjusted for different cable dimensions and different winding patterns. Equally important is that both linear and circular stators of different sizes can be wound with the same production technique.
4. Suggested developed automation solution

In this section the suggested developed automation solution for cable winding is presented together with the design and the constructed prototype of an essential winding tool used in this solution.

4.1. Basic conceptual automation method choices

None of the existing stator winding automation techniques for conventional machines described in Section 3.1 can be implemented for cable wound machines, mainly because the existing techniques are not able to deal with cables and feed them through the stator. Therefore another winding method is required. The work presented in this article will focus on the conceptual cable winding method described in [38], since this concept has the potential to deal with the requirements presented in Section 3.4. To push and pull a cable through the stator during winding, a cable feeder must be used. Preferably one cable feeder is used on each side of the stator so that the cable end can always be caught when being pushed through from the opposite side. Some of the demands on this cable feeder are that it must be capable to create and transfer a high enough feeding force to the cable, it must be able to catch, hold and let go of the cable, it must be able to direct the cable straight into the stator slots, it must not damage the cable, it must be possible to position it close to the stator sides without colliding with completed end windings and it should have the capability to push down end windings blocking a stator slot. Further, it should be possible to position the cable feeder against the stator sides with high accuracy, so that it can feed the cable straight into a slot and catch a cable coming out from a slot. A final requirement on the cable feeder is that it must be fairly easy to adjust within reasonable limits to different cable dimensions, stator sizes, stator shapes and winding patterns.
There are some cable feeders on the market today, but they are mostly designed to be used with large diameter cables. Consequently, these tools are often space consuming and lack options such as cable steering and the possibility to easily open up fully, which are essential for automated cable winding. No ideal feeder that can fulfill the requirements mentioned above has been found. Therefore a new cable feeder has been designed by developing an automated winding cell.
Since the cable cannot be fed through all the stator slots at the same time, a cable parking with temporary cable storages is needed. In addition, a cable supply from where new cable can be collected is needed together with equipment to prepare the cable

Fig. 6. Pure three phase wave winding pattern used as reference in this article. Note that this illustration is simplified compared to the UU WEC stator, for example there are eight slot holes per slot in the UU WEC stator.

Fig. 5. A cable wound UU WEC stator section mounted inside an UU WEC.

E. Hultman, M. Leijon / Robotics and Computer-Integrated Manufacturing 29 (2013) 246–256 | 249

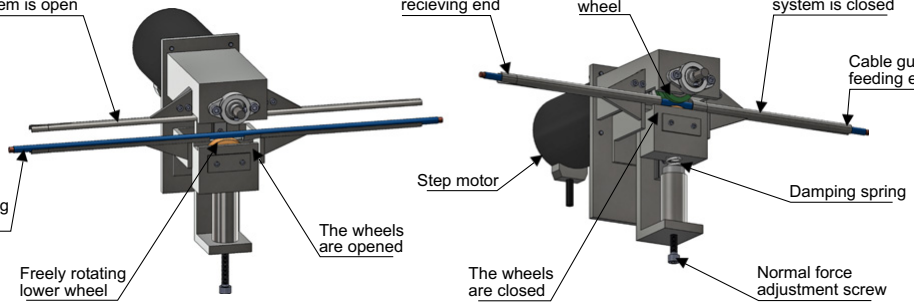
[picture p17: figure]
Freely rotating lower wheel; The wheels are opened; Damping spring; Normal force adjustment screw The wheels are closed; Step motor
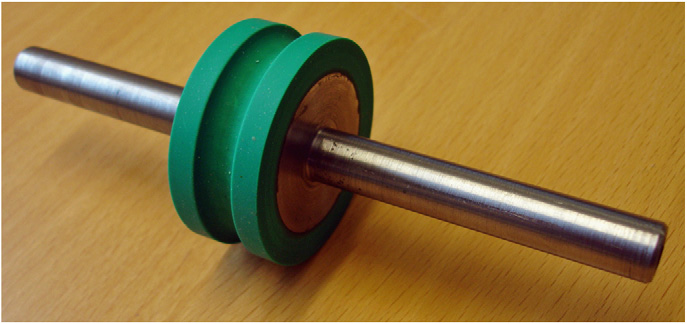
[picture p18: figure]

end so that it does not get stuck in the stator while being fed through.
The reasoning above indicates that a flexible positioning system with at least four degrees of freedom and a wide reach is needed to position the cable feeders. A natural solution to this is to use industrial robots holding cable feeder tools.
A robot cell layout for this cable winding automation solution has been developed and the final version is presented in Section 5.
4.2. Cable feeder tool design and prototype

A simple, controllable and compact cable feeder tool prototype, adjusted for robotized cable winding, has been designed and constructed. The final cable feeder design, main components and its working principle are shown in Fig. 7.
The feeder uses a single feeding wheel, driven by a step motor, to transfer a high feeding force from the motor to the cable. A freely rotating second wheel is then mounted below the driven wheel. By adding mechanics so that the lower wheel can be moved against and away from the upper wheel, the cable feeder is then able to grab the cable between the two wheels and to feed the cable. In order to maximize the frictional force against the cable, the outer part of the feeding wheel was made of high-friction rubber with a well defined radius, see Fig. 8. To reach a high normal force between the cable and the driven wheel, allowing higher feeding forces without slipping, the lower wheel is able to push the cable against the driven wheel with a pre-defined force. The position of the lower wheel is changed manually by rotating a screw at the bottom of the feeder. Since the cable’s outer diameter is not perfectly constant, the second wheel is coupled to a spring that keeps the force on the cable fairly constant by adjusting for deviations in cable diameter. Hence, the positioning screw for the lower wheel can be used to adjust the normal force on the cable.
Through experiments it was decided that the cable feeding force must be around 250 N to ensure uninterrupted winding of an UU WEC stator section. The required force varies substantially from slot to slot depending on the wear of the cable, the small irregularities in the cable diameter and on how well the stator sheet slots are aligned to each other. The static friction coefficient between the winding cable PVC insulation and the feeding wheel was experimentally determined to about 0.9.
An important feature of the feeder tool is the cable guiding system, whose main function is to direct the cable into, through and out of the feeder. The guiding stretches about 200 mm from each side of the wheels and has three different operating modes. To begin with, it is possible to open up the guiding together with the wheels, thus enabling the feeder to drop the cable. Secondly the guiding can be closed while the wheels are opened so that the cable can be directed and fed through the feeder, and finally, the guiding can be closed together with the wheels in order to fix the cable between the wheels and enable cable feeding. One side

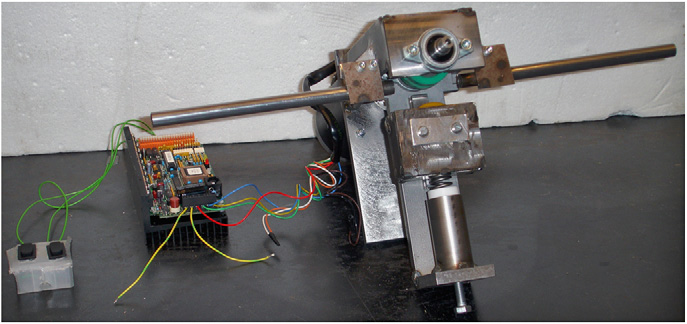
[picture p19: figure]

of the cable guiding, the receiving end, is adjusted for receiving the cable by adding a funnel at the end of the steering and thereby facilitating the cable end to be directed into the feeder. The other side of the guiding, the feeding end, is designed as a narrowing cone that facilitates precise steering of the cable into a stator slot hole. The same principle was used on the inner sides of the guiding system to ease feeding of a cable through the cable feeder, between the two wheels.
A full-scale cable feeder tool prototype was constructed, identical to the described design apart from the fact that the cable guiding system was simplified and not possible to open, see Fig. 9.
5. Robot cell layout and simulation results

This section presents the suggested final robot cell layout for stator cable winding automation and the offline robot programming experiments performed in ABB RobotStudio.
A robot cell offline simulation was built and used during the development of a functional automated cable winding production cell to validate its function. To minimize the winding cycle time of an UU WEC stator section, four ABB IRB4400/60 kg robots were

The cable guiding
system is open

Winding
cable

Cable guiding
recieving end | Feeding wheel

The cable guiding
system is closed

Cable guiding
feeding end

Fig. 7. Designed cable feeder tool and its components, in cable-drop position to the left and in feeding position to the right.

Fig. 8. High-friction feeding wheel used in the constructed cable feeder prototype.

Fig. 9. Constructed cable feeder tool prototype.

250 | E. Hultman, M. Leijon / Robotics and Computer-Integrated Manufacturing 29 (2013) 246–256

used in one production cell, see Fig. 10. The robots were programmed to work together, interacting and controlling tools and other equipment and sensors through digital signals. The simulated work procedure could also be used to estimate the total winding cycle time.
The winding of a cable starts from the middle of the stator section, from the middle of a cable and is done in two directions simultaneously by the two robot pairs. About 700 m of cable is used for the stator winding. A three-phase winding pattern is used and the total cable length is divided into 24 cables, each stretching over the full stator length. The cable sections are then connected to each other at the ends of the stator section.
The robot cell winding procedure starts with an unwound WEC stator section being automatically fed into the robot cell and fixed between the robots. Using positioning sensors on the cable feeder tools, the robots can then measure the exact stator section position. In this way, a less exact stator section positioning in the cell is required. The winding begins as one robot picks up the cable end from the cable drum. The cable drum setup is equipped to hold and prepare the cable end and feed cable from the drum. Next, the cable is fed through the stator section and then picked up on the other side by the co-operating robot. Using a temporary cable storage, the cable end can be parked while the full length of the cable is fed through and then picked up again by the second robot. Again, the cable is fed through the stator section and the first robot picks up the cable end. The cable is then immediately fed back through the next to-be-wound slot hole in the stator section and the second robot parks the cable on another shelf in the temporary storage. This way, by using both robots to pull the cable on both stator sides at the same time, the cable can be fed through two slots simultaneously and the winding cycle time is reduced considerably. This winding operation principle is repeated until the whole cable is wound, after which the next cable is wound until the winding is completed. When the winding is completed, the finished stator section is automatically fed out from the robot cell in the opposite direction from where it was originally fed in, creating an easily implementable production flow. Fig. 11 shows a summary of the winding method described above.
The performed robot cell simulation validated that the selected robots, equipped with cable feeder tools, could carry out all necessary movements and positioning to achieve the suggested winding procedure. It was also confirmed that the cable feeder tool geometry design is suitable for the winding operation.
6. Experimental results

This section presents the experiments and calculated results from the different experiments using the constructed cable feeder tool and an industrial robot together with the results from Section 5.

6.1. Cable feeder prototype experimental winding results

Experiments with the constructed cable feeder tool validated the feeding and guiding functions of the cable feeder. The feeder tool prototype was used to both push and pull the cable through a full-scale UU WEC stator section using the experimental set-up shown in Fig. 12. Cable feeding velocities of up to 0.5 m/s through the stator section and up to 2 m/s feeding the cable through the feeder only were performed successfully. The normal force on the cable was set manually to prevent the cable from slipping against the feeding wheel. The use of a damping spring in order to keep a fairly constant normal force on the cable showed to be a really helpful function. The cable guiding system used to steer the cable though the feeder and straight into a stator slot hole proved to be very useful, avoiding buckling and wear of the cable and thereby

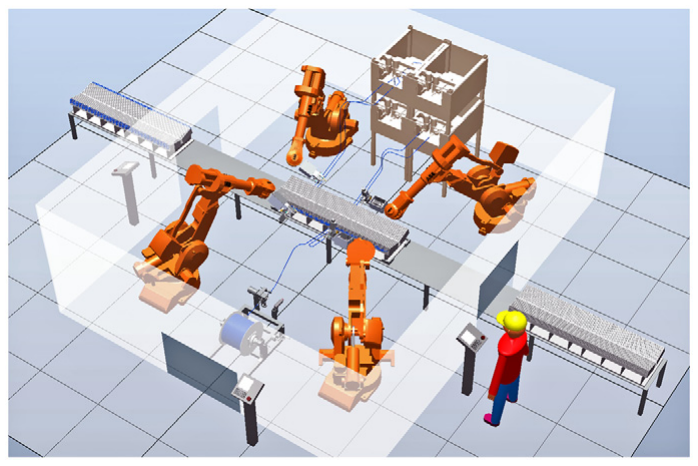
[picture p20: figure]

Fig. 10. A simulation of the suggested automated cable winding cell in ABB RobotStudio.

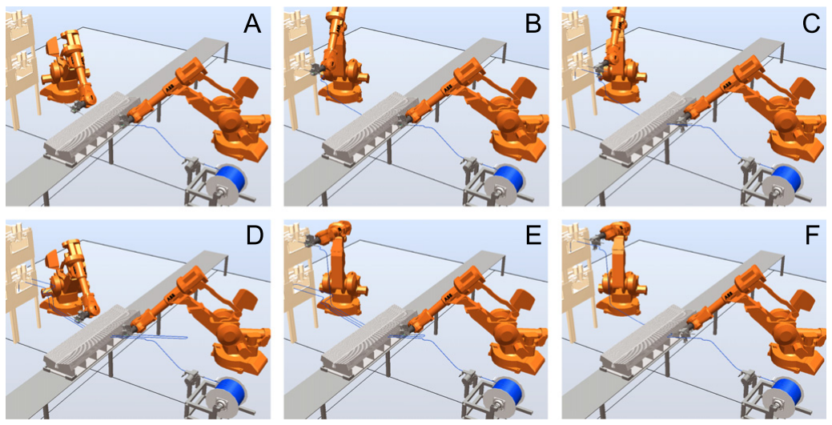
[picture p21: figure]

Fig. 11. A summary of the suggested robotized cable winding method, with one of the two robot pairs in one production cell. The cable is delivered from the cable drum holder and a cable parking is used to enable cable winding through two slots simultaneously. The process goes from step (A)–(F) and is repeated until all the slots are wound, after which a new cable is wound until the whole stator section is wound.

E. Hultman, M. Leijon / Robotics and Computer-Integrated Manufacturing 29 (2013) 246–256 | 251

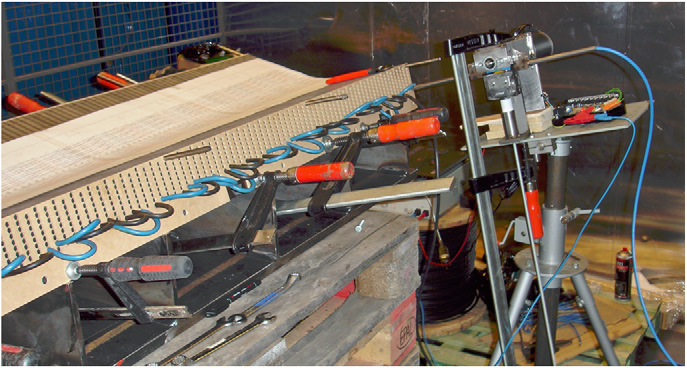
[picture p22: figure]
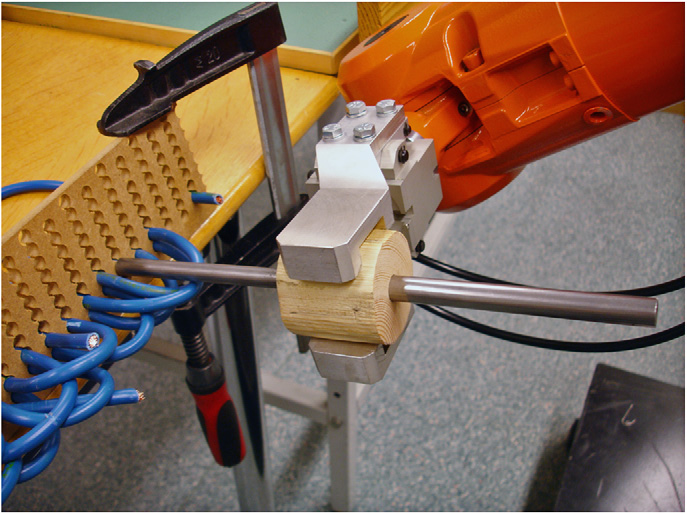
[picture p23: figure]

greatly facilitating pushing the cable through the stator section. Another benefit of using a cable feeder tool was that a constant cable feeding velocity, with a controlled maximum velocity, reduced the wear of the cable. An important result of this characteristic is that melting of the cable insulation as a cable is fed against an end winding can be avoided by keeping a high feeding velocity but avoiding the short extreme velocities that can occur during manual winding.
Finally, it was understood through the experiments that a cable feeder tool for robot winding must be robust and precise, both in construction and positioning, and enable a high normal force and a high feeding force on the cable. In addition, a sensorbased control system that can prevent the feeder from occasionally slipping against the cable might be a useful function for further experiments and development of the feeder tool.
The experiment thus both validated all the functions of the cable feeder tool prototype and suggested some future tool improvements.
6.2. Experimental winding method and robot positioning validations

An ABB IRB1400/5 kg M98 S4C industrial robot equipped with a cable feeder tool dummy was used for robot positioning experiments against an UU WEC stator section dummy, see Fig. 13. Within these experiments, it was validated that the industrial robot could provide the required positioning accuracy for the suggested cable winding automation method. This experiment also proved the functions to direct the cable end into a stator slot hole, to position the cable guiding system against a stator section side and to push away earlier wound end windings. Robot tool and work object coordinate systems were defined and the robot was programmed to move between the stator slot holes using these coordinate systems and offset values to simulate a three-phase cable winding pattern. All simulated movements from ABB RobotStudio were validated, only without the full reach of an ABB IRB4400/60 kg robot.

6.3. Winding cycle time

From the results of the robot cell winding simulation and the winding experiments with the constructed cable feeder tool prototype, the winding cycle time for one UU WEC stator section can be calculated. The total winding cycle time will be divided into robot positioning time and cable feeding time, while cable end connecting and stator section transportation will be neglected. By analyzing the developed winding procedure in the robot cell simulation, it turns out that each robot pair must perform about 1800 positioning tasks during the winding of one stator section. A reasonable approximation from the robot cell simulation is that one such movement, including feeder tool tasks, takes on average four seconds to perform. Some examples of positioning tasks are to collect the cable end at the cable parking and position against a stator slot hole, to collect a cable that is fed through the stator section and position against the next slot hole, to drop a cable and position against a slot hole or to park a cable end at the cable parking. Positioning operations that can be performed simultaneously by both robots are counted as a single positioning. From this, the total robot positioning time during the winding of one stator section can be approximated to about 130 min, including additional operations such as preparing the cable end and measuring the position of the stator section. Next, the total cable feeding time must be calculated. Since the robots work in pairs, it is important to separate between when the cable is fed through only one slot hole and when it is fed through two slot holes simultaneously. It is desired that the feeding should be done through two slots at the same time whenever possible, but during some winding operations this cannot be done. From the winding procedure explained in Section 5, it can be understood that these operations are when the cable end has been picked up at the parking and is fed through the stator section, when the cable is fed back through the stator and parked again and finally as the end windings on the cable drum stator section side are formed. Table 1 presents approximations of the necessary winding parameters for calculating the total cable feed length during the winding of one UU WEC stator section. The total feeding length per winding cable is calculated from the suggested robot winding principle. During the first and last feeding operations, the cable is fed through a single slot hole only, while the other operations utilize the cable parking to feed the cable through two slot holes simultaneously. For the last slot holes to be wound the cable parking cannot be used, this is however neglected in these calculations.
The total length of cable that must be fed by one robot pair during the winding of one stator section, i.e. the total cable feeding length, is easily approximated from the parameters in Table 1 to be about 2500 m. From the cable feeder tool prototype winding experiment, it was concluded that a reasonable cable feeding velocity through the stator section is about 0.5 m/s. The total winding cycle time can now be calculated using Eq. (3), where ttot is the total winding cycle time, lfeed is the total cable feeding length per UU WEC stator section and robot pair, vfeed is the average cable feeding velocity and tpos is the total robot positioning winding cycle time.

ttot ¼ lf eed

vf eed

þtpos | ð3Þ

Fig. 12. Experimental setup used for validating the cable feeder tool function with a full scale UU WEC stator section.

Fig. 13. Cable feeder tool dummy and the stator dummy used with an ABB IRB1400 robot in positioning experiments.

252 | E. Hultman, M. Leijon / Robotics and Computer-Integrated Manufacturing 29 (2013) 246–256

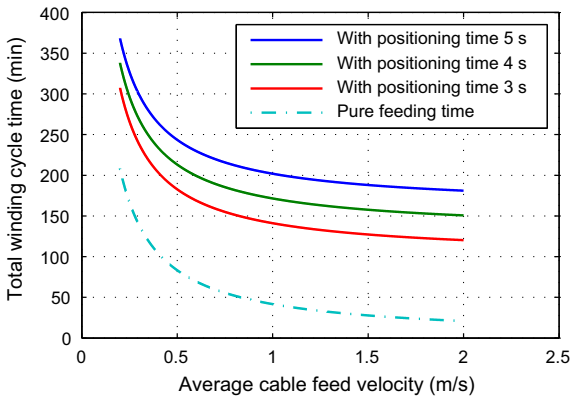
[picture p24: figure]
Average cable feed velocity (m/s); Total winding cycle time (min); With positioning; time 5 s; Pure feeding time

The total winding cycle time results for some different average robot positioning times, as a function of cable feed velocity are shown in Fig. 14. Pure positioning time, as a function of cable feed velocity is also shown. For low cable feed velocities, the cable feeding time is the dominating part of the total winding cycle time, while positioning time is more important for high velocities. Faster robot positioning and higher winding feed velocities are both important tools to lower the total cycle time. A consistent first approximation is to use an average cable feeding velocity of 0.5 m/s, 4 s as average positioning time and the winding procedure explained in Section 5. This results in a total cycle time of about 215 min. In this case, the robot positioning time is longer than the cable feeding time.
Apart from speeding up the cable feeding and robot movements, one approach for optimizing the cycle time is to adjust the winding method, for example by pulling the cable through more slots at the same time using guiding wheels for the cable on the sides of the stator section or excluding the cable parking and feeding the cable through the slots one by one. It is even possible to change the winding pattern and number of winding phases, but this approach will of course also change the electromagnetic machine design. Fig. 15 shows the total winding cycle time, separated into positioning time and feeding time, with different winding methods and different winding patterns. Some important winding parameters for these approaches are shown in Table 2. Three-phase winding results in more but shorter cables to be wound, while one-phase winding results in fewer but longer cables, compared to the two-phase winding pattern. Both winding the cable slot-by-slot, without the cable parking function, and winding through four slots simultaneously reduces the number of robot positionings required. Slot-by-slot winding involves the fewest positionings and the longest total cable feed length, while four-slot winding has the shortest feed length for two-phase and three-phase winding patterns. For the chosen cable feed velocity and average positioning time, the shortest total winding cycle time of an UU WEC is reached using a three-phase winding pattern. In this case, the different winding methods give similar results. With two-phase and one-phase winding patterns, feeding the cable through more slot holes simultaneously lowers the total cycle time.
Manual winding of an UU WEC stator section, based on the stator design and three-phase winding pattern discussed in this article, has been performed at Uppsala University for two different WEC units, both with four stator sections each. All eight stator sections were manually wound by two personnel, resulting in a manual winding cycle time per stator section of about 40 h. An important observation from this manual production was that the winding task is very tiresome and boring for the workers. Experience from winding these stators, and from winding somewhat different stators for earlier UU WECs, implies that manual cable winding occasionally introduces human errors, especially when complicated winding patterns are used. These issues are essential arguments for automated cable winding.
6.4. Economical analysis

To make an economical analysis of automated winding, the total investment cost of one robotized cable winding production cell, as presented in this article, must be roughly estimated. The dominating cost unit is the industrial robots. It is likely that pre-owned robots of older models can be used for this task, thus reducing the total investment cost substantially. Approximations of the different cost units are shown in Table 3. From these costs, the total investment cost can be calculated to be about 282,000 EUR

Table 1
Approximations of winding length parameters and calculated feeding length results, per robot pair, for the suggested automated winding cell and one UU WEC stator section with a three-phase winding pattern.
Parameter | Value
Number of cables per stator section | 24 Cables
Average distance between cable parking and stator section | 1.5 m
Total length of one (half) winding cable | 12.6 m
Number of slot holes through which each cable is wound | 22 Slot holes
Cable length per slot hole penetration, including end winding 0.55 m
Extra cable winding length | 0.5 m
Total feeding length per winding cable | 104.15 m
Feeding length first feeding, through a single slot hole | 12.6 m
Feeding length second feeding, through two slot holes | 14.0 m
Feeding length third feeding, through two slot holes | 12.9 m
Feeding length fourth feeding, through two slot holes | 11.8 m
Feeding length fifth feeding, through two slot holes | 10.7 m
Feeding length sixth feeding, through two slot holes | 9.6 m
Feeding length seventh feeding, through two slot holes | 8.5 m
Feeding length eight feeding, through two slot holes | 7.4 m
Feeding length ninth feeding, through two slot holes | 6.3 m
Feeding length tenth feeding, through two slot holes | 5.2 m
Feeding length eleventh feeding, through two slot holes | 4.1 m
Feeding length twelfth feeding, through a single slot hole | 1.05 m
A | B | C | D | E | F | G | H | I

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
Winding scenario

Total winding cycle time (min)
Feeding time
Positioning time

Fig. 15. Total winding cycle time for some different winding scenarios, separated into positioning and feeding time. Scenario (A), (B) and (C) are for three-phase winding pattern, while (D), (E) and (F) are for two-phase winding and (G), (H) and (I) are for one-phase winding. Scenarios (A), (D) and (G) represent winding slot-by-slot, while (B), (E) and (H) represent winding through two slots simultaneously and (C), (F) and (I) represent winding through four slots simultaneously. All scenarios are using 0.5 m/s average cable feed velocity and 4 s average positioning time.

| With positioning With positioning | time 4 s time 3 s

Fig. 14. Calculated total winding cycle times for one UU WEC stator section with the suggested automated winding cell for different positioning times, as a function of cable feed velocity. The dotted line represents feeding time only. All results are based on a three-phase wave winding pattern and the suggested winding method through two slots simultaneously.

E. Hultman, M. Leijon / Robotics and Computer-Integrated Manufacturing 29 (2013) 246–256 | 253

using new robots and about 182,000 EUR using older robots. However, the following calculations will assume that new robots are used.

The production of one automated robot cell, one stator section per 215 min, should be compared to the production through manual winding, one stator section per 20 h with four personnel. This gives a rough approximation that the production of one robotized winding cell is equal to the production of about 5.5 manual winding cells. By comparing the investment and running costs for one automated robotized winding cell to the running costs for 5.5 manual winding stations, an economical evaluation of the robot cell can be performed. The cost parameters for both manual and automated winding are presented in Table 4. The investment cost for a manual winding cell is neglected.
Using Eq. (1), the net present value of the winding automation investment, compared to manual winding, can be calculated to about 7,000,000 EUR. The payback period, compared to manual winding, can be calculated from Eq. (2) to about two months. Fig. 16 shows the total cost per year, divided into major cost units, for manual and automated cable winding. The dominating cost difference between manual and automated cable winding is the personnel cost, which is very high with manual winding. Fig. 17 shows the accumulated costs and cost difference for manual and automated cable winding during the economical lifetime of the robot cell investment.
7. Conclusions

Using cable winding technology in electric machine stators is likely to facilitate automated production compared to using conventional winding techniques. Production steps such as pre-insertion of insulation in the stator slots, possible insertion of pre-wound coils into the stator slots and winding fixation are eliminated and the need for connecting end windings is reduced compared to conventional windings. Apart from the electrical benefits of cable wound machines, the concept is also suitable for automated production.
Previous research indicates that automated stator winding in production is an important but at the same time complex field. Automation methods for stator winding of conventional electric machines have been developed and implemented in production lines for many years. However, since cable wound stators are not very common today, a published method to automate cable winding has not been found. Advances in robot technology, together with high flexibility demands, make industrial robots suitable for implementation in a solution to this problem. Existing winding automation methods for conventional stator winding cannot be used for cable winding automation.
A production method using industrial robots for automation of cable winding of electric machines has been suggested in this article.

Table 2
Winding and positioning parameters, per robot pair, for automated winding of one UU WEC stator section with different winding methods and winding patterns.
Parameter | Value
Number of cables per stator section one-phase winding | 24
Number of cables per stator section two-phase winding | 16
Number of cables per stator section three-phase winding | 8
Total feeding length per winding cable one-phase, slot-by-slot winding | 1249 m

Total feeding length per winding cable one-phase, two-slot winding 717 m Total feeding length per winding cable one-phase, four-slot winding 521 m
Total feeding length per winding cable two-phase, slot-by-slot winding | 325 m

Total feeding length per winding cable two-phase, two-slot winding 207 m Total feeding length per winding cable two-phase, four-slot winding 184 m
Total feeding length per winding cable three-phase, slot-by-slot winding | 150 m

Total feeding length per winding cable three-phase, two-slot winding 104 m
Total feeding length per winding cable three-phase, four-slot winding | 106 m
Number of positionings one-phase, slot-by-slot winding | 1064
Number of positionings one-phase, two-slot winding | 1816
Number of positionings one-phase, four-slot winding | 1432
Number of positionings two-phase, slot-by-slot winding | 1072
Number of positionings two-phase, two-slot winding | 1856
Number of positionings two-phase, four-slot winding | 1472
Number of positionings three-phase, slot-by-slot winding | 1080
Number of positionings three-phase, two-slot winding | 1824
Number of positionings three-phase, four-slot winding | 1464

Table 3
Investment cost by cost units for the presented automated winding cell.
Cost unit | Investment cost | Number of units

Total cost

New industrial robot | 50,000 EUR | 4 | 200,000 EUR
Pre-owned industrial robot | 25,000 EUR | 4 | 100,000 EUR
Cable feeder robot tool | 8000 EUR | 4 | 32,000 EUR
Cable drum holder | 5000 EUR | 1 | 5000 EUR
Cable parking | 20,000 EUR | 1 | 20,000 EUR
Stator section feeding and positioning table | 10,000 EUR | 1 | 10,000 EUR
Cell enclosure, safety, control and installation | 15,000 EUR | 1 | 15,000 EUR

Table 4
Cost parameters for both manual winding and the suggested automated winding cell.
Parameter | Winding cell | Value
Winding personnel cost | Manual winding | 20 EUR/h
Number of personnel per winding station | Manual winding | 4
Factory floor space per winding station | Manual winding | 12 m²
Winding personnel cost | Automated winding | 30 EUR/h
Number of personnel | Automated winding | 0.5
Factory floor space | Automated winding | 32 m²
Power consumption | Automated winding | 60 kW
Yearly robot and cell equipment maintenance cost | Automated winding | 30,000 EUR
Investment economical lifetime | Automated winding | 5 years
Investment discount rate | Automated winding | 4%
Robot cell installation and commissioning cost | Automated winding | 25,000 EUR
Investment cost | Automated winding | 282,000 EUR
Investment rest value | Automated winding | 75,000 EUR
Number of manual stations per automated winding cell | Common parameter | 5.5
Factory floor space cost | Common parameter | 0.1 EUR/m² /h
Electricity cost | Common parameter | 0.1 EUR/kWh
Yearly winding production time | Common parameter | 4000 h
254 | E. Hultman, M. Leijon / Robotics and Computer-Integrated Manufacturing 29 (2013) 246–256

The function of the method has been validated by computer simulations, robot positioning experiments and experiments using a constructed cable feeder tool prototype to feed cable through a stator. Using a linear, cable wound UU WEC generator stator section as an example, considerably production time and production cost savings are indicated compared to manual winding. However, manual cable winding is not performed today in serial production. An economical analysis comparing manual and automated cable winding can therefore only investigate two hypothetical cases. Since manual cable winding is a very personnel-intensive and time consuming task, it is also very costly and thus not suitable for large scale production. The automated winding solution suggested in this article does as a result have a very high net present value and short payback period compared to the hypothetical manual winding case. The suggested method is adapted to fit into a production line and is very flexible in order to make it possible to use this method for many different cable wound electric machines. For example, cable wound stators of different sizes, shapes, with different cable dimensions and with different winding patterns can be handled. For this, only small adjustments to the feeder tool is needed, mainly regarding the cable guiding size, the feeding wheel size and the feeder motor torque. Also, different robot models can be used and the robot programming is easily changed to different winding scenarios. For stator winding with cables of a much larger diameter than the cable used in the UU WEC example in this article, the cable feeder tool feeding mechanism may need to be adjusted for much higher feeding forces and larger cables.

More work is needed to improve the cable feeder tool, e.g. adding sensors to supervise and facilitate the winding, to construct side equipment and more. There is a large potential to reduce the winding cycle time further within the suggested winding automation, for example by increasing the cable feed velocity through the stator, improving the winding procedure and reducing the feeder tool operation time and robot positioning time. When deciding on a suitable cable winding automation method and adjusting the winding parameters, aspects such as desired winding pattern, cable lengths, cable wear and method complexity must be considered as well. However, if an automation method for cable winding is developed further and prepared for industrial implementation, this will be an important improvement of the production of direct drive machines, such as the Powerformer. Automated cable winding should then be more carefully compared to conventional stator winding production. Some interesting areas for the application of such machines are wind power [39–42], hydropower [43,44], wave power [36,37], thermal power [43] and high-voltage motors [45–47].

Acknowledgments

The authors are grateful to Magnus Rahm, Boel Ekergard and ˚ Marcus Linder for proof reading of this article. The authors would also like to thank Swedish Research Council grant no. 621-2009-3417 for the support of the project.

References

[1] Kirkhoff JR. Automation in electric motor stator processing. Coil Winding International 1980;4:4–9.
[2] Leimbach WB, Marshall JW. Automated stator and field winding. Electrical Manufacturing 1988;2:13–4.
[3] Mueller R. Automation and flexible design of coil winding. Wire World International 1985;27:22–5.
[4] Ferloni A, D’Ascanio R. Towards the automated factory: automation of a large series production line of generators for automobiles and industrial vehicles. In: Proceedings of the 14th international symposium on industrial robots and the 7th international conference on industrial robot technology; 1984. p. 315–21.
[5] Nakahara Yuji, Kasuga Yoshio, Azuma Ken-ichi, Kiri Shuichi, Takekoshi Yukinori. Fully automated production of the new ventilation fan motor. In: Proceedings of the 1992 Japan–USA symposium on flexible automation part 2; 1992. p. 1643–6.
[6] Reed WD. Self-bonding wire in automated motor assembly. In: Proceedings of the electrical insulation conference and electrical manufacturing and coil winding technology; 2003. p. 579–81.
[7] Itagaki T, Hiwasa H, Haga K. Design and manufacturing technology of Fuji electric’s large-capacity air-cooled turbine generator. Challenges of Power Engineering and Environment 2007;1–2:395–9.
[8] Morreale P. Electric motor and generator manufacturing myths. In: Proceedings of the 2007 electrical insulation conference and electrical manufacturing expo; 2008. p. 413–7.
[9] Reiger AC. Design considerations to facilitate winding and automation of two pole stators. Coil Winding International 1980;4:4–8.
[10] Leijon M, Owman F, Sorqvist T, Parkegren C, Lindahl S, Karlsson T. Power-Former(R): a giant step in power plant engineering. In: Proceedings of the IEEE international electric machines and drives conference; 1999. p. 830–2.
[11] Leijon M, Dahlgren M, Walfridsson L, Ming Li, Jaksts A. A recent development in the electrical insulation systems of generators and transformers. IEEE Electrical Insulation Magazine 2001;17:10–5.
[12] Leijon M, Owman F, Johansson SG, Karlsson T, Lindahl S, Parkegren C, et al. Powerformer(TM)—the prototype and beyond. Power Engineering Society Winter Meeting 2000;1:139–44.
[13] Dettmer R. The heart of a new machine. IEE Review 1998;44:255–8.
[14] Metwally IA, Radwan RM, Abou-Elyazied AM. Powerformers: a breakthrough of high-voltage power generators. IEEE Potentials 2008;27:37–44.
[15] Hooshyar H, Savaghebi M, Vahedi A. Synchronous generators: past, present and future. In: Proceedings of the AFRICON 2007; 2007. p. 1–6.
[16] Jiang X, Koo K, Kikuchi K, Konno A, Uchiyama M. Robotized assembly of a wire harness in car production line. In: Proceedings of the 2010 IEEE/RSJ international conference on intelligent robots and systems; 2010. p. 490–5.
[17] Shirizadeh B, Foong Chee Wei, Tan Boon Hui. Robotic fibre placement process planning and control. Assembly Automation 2000;20:313–20.
[18] Gomez Ortega J, Gamez Garcia J, Satorres Martinez S, Sanchez Garcia A. Industrial assembly of parts with dimensional variations. Case study:
Manual winding | Automated winding

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
Cost per year (million EUR)

Personnel cost
Floor space cost
Electricity cost Maintenance cost

Investment cost

Fig. 16. Yearly cost for manual and automated cable winding, divided into major cost units and compared as described in Section 6.4.

0 | 1 | 2 | 3 | 4 | 5

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
Year after commissioning

Accumulated sum (million EUR)
Manual | winding cost
Automated winding cost
Cost savings

Fig. 17. Accumulated costs and cost difference for manual and automated cable winding during the economical lifetime of the robot cell investment, compared as described in Section 6.4.

E. Hultman, M. Leijon / Robotics and Computer-Integrated Manufacturing 29 (2013) 246–256 | 255

assembling vehicle headlamps. Robotics and Computer-Integrated Manufacturing 2011;27:1001–10.
[19] Uchida H, Amemiya Y. FANUC—the planning and development of a highly advanced robotized production system for servo motors. Assembly Automation 1998;18:270–4.
[20] Gravel D., Maslar F, Zhang G, Nidamarthi S, Chen H, Fuhlbrigge T. Toward robotizing powertrain assembly. In: Proceedings of the 2008 7th world congress on intelligent control and automation; 2008. p. 541–6.
[21] Yao W, Cannella F, Dai JS. Automatic folding of cartons using a reconfigurable robotic system. Robotics and Computer-Integrated Manufacturing 2011;27: 604–13.
[22] Teresko J. New roles for robotics. IndustryWeek (IW) 2005:25–32.
[23] Mortimer J. Jaguar lifts XF robot total to 179. Industrial Robot 2009;36: 114–20.
[24] Mortimer J. BMW lifts robot total to 500 at Plant Oxford. Assembly Automation 2008;28:27–35.
[25] Gravel DP. Flexible robotic assembly efforts at Ford Motor Company. In: Proceedings of the 2003 IEEE/RSJ international conference on intelligent robots and systems; 2003. p. 2522–7.
[26] Pietropaoli L. How to evaluate justify stator winding automation. Electrionics 1987;33:22–3.
[27] Connolly C. Technology and applications of ABB RobotStudio. Industrial Robot 2009;36:540–5.
[28] Mumford DW. In-slot winding of DC brushless motors. In: Proceedings of the electrical insulation conference and electrical manufacturing & coil winding technology conference; 2003. p. 89–92.
[29] Mecrow BC, Jack AG, Haylock JA, Hoefer U, Dickinson PG. Simplifying the manufacturing process for electrical machines. IEE Conference Publication 2004;1:169–74.
[30] Ishigami T, Kitamura M, Sanada K. Stator-core structure and winding technology for EPS motors. Electrical Engineering in Japan 2011;175:35–42.
[31] Jack AG, Mecrow BC, Dickinson PG, Stephenson D, Burdess JS, Fawcett N, et al. Permanent-magnet machines with powdered iron cores and prepressed windings. IEEE Transactions on Industry Applications 2000;36:1077–84.
[32] EL-Refaie AM. Fractional-slot concentrated-windings synchronous permanent magnet machines: opportunities and challenges. IEEE Transactions on Industrial Electronics 2010;57:107–21.
[33] Akita H, Nakahara Y, Miyake N, Oikawa T. New core structure and manufacturing method for high efficiency of permanent magnet motors. In:

Proceedings of the conference record of the industry applications conference 38th annual meeting. vol 1; 2003. p. 367–72.
[34] Kawamura T, Shimaru M, Nakazawa M, Sasahara M, Kobayashi K, Kojima T. Study on high precision winding of toroidal coil and automation of its process. In: Proceedings of the IEEE/ASME international conference on advanced intelligent mechatronics. vol. 1; 2001. p. 654–8.
[35] Alfredson S, Hernnas B, Bergstr ¨ | om H. Assembly of generators with rated ¨
voltage higher than 100 kV. In: Proceedings of the 2000 international conference on power system technology. vol. 1; 2000. p. 189–93.
[36] Leijon M, Bostrom C, Danielsson O, et al. Wave energy from the north sea: ¨ experiences from the Lysekil research site. Surveys in Geophysics 2008;29: 221–40.
[37] Danielsson O, Eriksson M, Leijon M. Study of a longitudinal flux permanent magnet linear generator for wave energy converters. International Journal of Energy Research 2006;30:1130–45.
[38] Backlund A, Leijon M. Forfarande och anordning f ¨ | or montering av en stator- ¨
lindning bestaende av en kabel. [SE508544]. Sweden; 1998. ˚
[39] Dahlgren M, Frank H, Leijon M, Owman F, Walfridsson L. Windformer(TM): wind power goes large-scale. ABB Review 2000;3:31–7.
[40] Anonymous. Revolution in the wind. Modern Power Systems 2000;20(63):65.
[41] Marko S, Darul’a I. Wind energy. Journal of Electrical Engineering 2003;54: 329–31.
[42] Eriksson S, Solum A, Leijon M, Bernhoff H. Simulations and experiments on a 12 kW direct driven PM synchronous generator for wind power. Renewable Energy 2008;33:674–81.
[43] Leijon M, Johansson SG, Owman F, Alfredson S, Karlsson T, Lindahl S, et al. Powerformer(TM)—experiences from the application of extruded solid dielectric cables in the stator winding of rotating machines. In: Proceedings of the 2000 IEEE power engineering society winter meeting. vol. 1; 2000. p. 736–44.
[44] Yuen K, Thomas K, Grabbe M, Deglaire P, Bouquerel M, O¨ sterberg D, et al. Matching a permanent magnet synchronous generator to a fixed pitch vertial axis turbine for marine current energy conversion. IEEE Journal of Oceanic Engineering 2009;34:24–31.
[45] Eriksson G. Motorformer(TM): a new motor for direct HV connection. ABB Review 2001;1:22–5.
[46] Nestli TF, Stendius L, Johansson MJ, Abrahamsson A, Kjaer PC. Powering Troll with new technology. ABB Review 2003;2:15–9.
[47] Bartos FJ. ‘Real’ high voltage motors are here. Control Engineering 2004;51: 36–40.
256 | E. Hultman, M. Leijon / Robotics and Computer-Integrated Manufacturing 29 (2013) 246–256

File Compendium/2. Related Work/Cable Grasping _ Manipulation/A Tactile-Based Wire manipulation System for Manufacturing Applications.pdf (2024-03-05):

# robotics (http://www.mdpi.com/journal/robotics)

Article

# A Tactile-Based Wire Manipulation System for Manufacturing Applications

Gianluca Palli 1,† and Salvatore Pirozzi 2,*

,†

1 | Università di Bologna—DEI, Viale del Risorgimento 2, 40136 Bologna, Italy; gianluca.palli@unibo.it
2 | Università degli Studi della Campania—DI, Via Roma 29, 81031 Aversa (CE), Italy
* | Correspondence: salvatore.pirozzi@unicampania.it; Tel.: +39-081-5010-433
† The authors contributed equally to this work.

Received: 9 April 2019; Accepted: 10 June 2019; Published: 12 June 2019

(http://www.mdpi.com/2218-6581/8/2/46?type=check_update&version=1)

Abstract: This paper presents experimental results developed within the WIRES experiment, whose main objective is the robotized cabling of switchgears. This task is currently executed by human operators; the WIRES Project tackles the development of a suitably designed sensorized end effector for the wire precise manipulation. In particular, the developed gripper with tactile sensors are shown and a procedure for the implementation of the insertion task is presented and discussed. Experimental results are reported both for quality of wire shape reconstruction and success rate of insertion task implementation.

Keywords: tactile sensors; manipulation task; assembly robot

### 1. Introduction

Robotic manipulation is a complex task especially when deformable and fragile objects have to be grasped. In these cases, the knowledge of geometrical and physical characteristics of the object to manipulate are fundamental for the successful implementation of the task. To this aim, specific sensing systems are developed to be integrated into robotic systems. This paper presents results of activities developed within the WIRES experiment (http://www-lar.deis.unibo.it/people/gpalli/WIRES/), where the main objective is the robotized cabling of switchgears. Switchgears are basic components in a wide range of applications. Currently, the switchgear wiring is executed by human operators due to the complex manipulation tasks. The WIRES Project tackles the development of a suitably designed end effector equipped with a vision system and a tactile sensor for wire-precise manipulation. Preliminary results have been presented in [1–3].
Standard approaches to this kind of problem use vision and/or tactile data. Often vision is used alone due to its efficiency in data collection ([4]). However, this solution may fail in the presence of varying lighting conditions and occlusions. The use of tactile sensors helps to improve the success rate by overcoming some environment limitations. As a consequence, there have been many papers where vision and tactile data are integrated in a single approach ([5–9]. The objective of these approaches is the estimation of object characteristics, such as pose, shape, surface features and so on. Among these, some researchers propose interesting algorithms for edge detection [10] that could be considered in future as alternative approaches with respect to the one proposed here in order to improve the estimation quality. At the moment, the estimation quality reached with the approach proposed here is sufficiently high for the task implementation, with a very simple formalization. Some researchers in recent papers [11] use vision systems directly integrated into fingers to evaluate both tactile and image data at the same time and with the same sensing system. Also, this approach demonstrates how the fusion among tactile and vision data can be a good approaches for manipulation tasks. However, none of these past papers tackle the estimation problem of shape and pose of flexible objects like wires.
Robotics 2019, 8, 46; doi:10.3390/robotics8020046 (http://dx.doi.org/10.3390/robotics8020046) | www.mdpi.com/journal/robotics

Robotics 2019, 8, 46 | 2 of 13

In previous papers [2,12], the authors presented details of the tactile sensor design and a possible use of tactile data for the reconstruction of the grasped wire shape and the use of the estimated shape for the implementation of an insertion task. In those papers, the model used for the wire was constituted by a quadratic function for the grasped area and a straight line for the part outside the tactile sensor pad. The sensor was mounted on a commercial gripper and preliminary insertion tests have been carried out on a single hole of an electric component fixed on the workbench, with the same wire grasped from a single position.
This paper presents improvements with respect to the previous system in terms of mechatronic solutions that are integrated and tested in a new scenario much closer to real cases. In particular, for this paper, the tactile sensor has been integrated into the final end-effector designed for the WIRES Project, presented and equipped with an electric screwdriver used to automatically complete the connection task. A simplified solution for the wire shape estimation is considered in order to allow its integration directly into the on-board microcontroller. This solution is a subset of that proposed in [12], but is explicitly formalized to be used with the final end-effector in the current study. The quality of the reconstruction has been re-evaluated with the new model, by redefining the quality metric according to the different model, in order to check if the considered simplification does not strongly affect the expected results. Finally, unlike previous papers, the whole system has been tested in a more complex scenario, by grasping, inserting and connecting a sequence of wires in a testing switchgear as shown in the video as supplementary.

### 2. The Tactile Sensor and the Gripper

The tactile sensor working principle and its design is detailed in [12]. Here, a brief recalling is reported (related to the integration in the gripper). Figure 1 reports some pictures of the developed sensor where the main components are highlighted. The 16 taxels constituted by the optoelectronic components with the deformable layer bonded above represents the transduction part for the sensor. The optical signals are converted in electric signals by using simple resistors and the obtained voltage signals are acquired with a standard Analogue-to-Digital converter. All details about the components integrated in the PCB are reported in [12]. For the integration into the gripper finger, a second PCB with a microcontroller has been developed and connected to the first one. The second PCB is completed by a voltage regulator and a standard connector, which allows to interface the tactile sensor with a standard USB-TTL serial cable. A suitably designed finger case has been realized in aluminum via a 3D printing technique and the extended PCB has been integrated inside this case. The thickness of the designed case is the smallest in order to allow the insertion of the finger among the switchgear components and wires already connected. The case allows a mechanical connection to the gripper by using two screw.
The end effector developed in the WIRES experiment for the implementation of the whole cabling process can be seen in Figure 2. The end effector integrates a 2D camera providing top view of the scene, an computer-controlled screwdriver (to tight the terminal screws) and a 4-DOFs gripper equipped with the tactile sensor. The end effector is also equipped with an integrated torque/controlled screwdriver with remote PLC control and process data recording capabilities (Kolver PLUTO3CA electric screwdriver + EDU2AE/TOP/E control unit). In the final process implementation, the robot arm is used to position the screwdriver tip on the terminal screw, and the FT sensor will be used to control the contact with the screw during the tightening. Therefore, the end effector will be held in an almost fixed position, just the screw motion during the tightening will be compensated. Consequently, the wire insertion will be performed by using the gripper DOFs only. It results that the FT sensor can be used to estimate the interaction between the screwdriver and the terminal screw, but it cannot be used during the insertion and for the wire tightening check, because the magnitude of the force generated by the wire contact is much lower than the one generated by the contact between the screwdriver and the screw, making the former indistinguishable. For this reason, the use of the tactile sensor installed into the gripper fingertips is fundamental also during the insertion and for the wire tightening check, in order to reach a suitable success rate.

Assembled pad bonded to the PCB

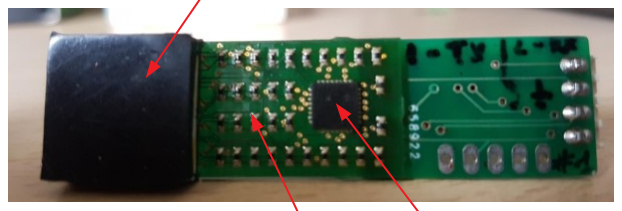
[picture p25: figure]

Resistors | A/D converter
(a)

Microcontroller

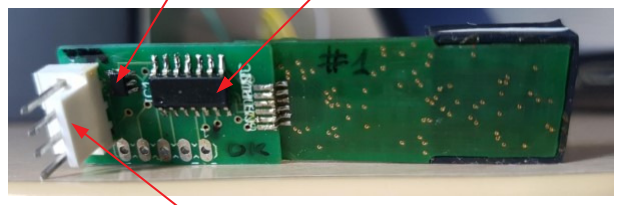
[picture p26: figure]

Connector

Voltage regulator

(b)

(c)

Figure 1. Some pictures of assembled tactile sensor: (a,b) report a front view and a rear view of the PCB components, respectively, while (c) reports the PCB integration into the gripper finger.

# 2D Camera

# Computer-Controlled

# Screwdriver

# Tactile

# Sensor

# Hydra Servo

# Controllers

# 4-DOF

# Gripper

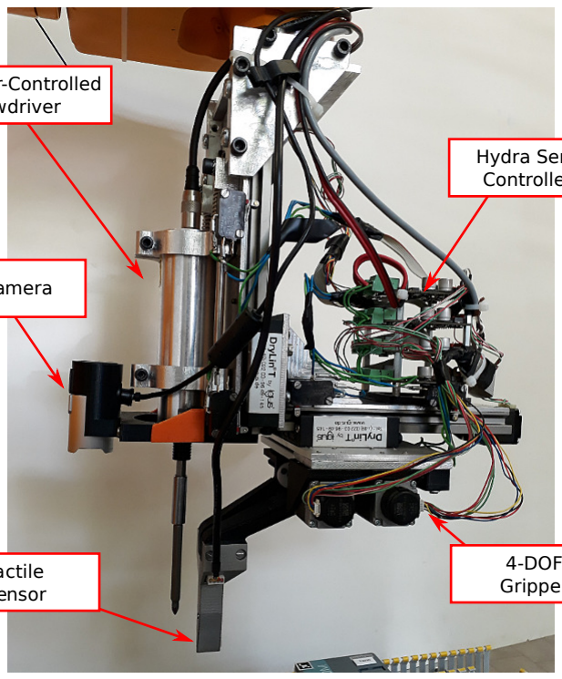
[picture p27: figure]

Figure 2. The end effector developed for the WIRES experiment. It is equipped with computer-controlled screwdriver, tactile sensor, 2D camera, Hydra servo controller boards, and a 4-DOF gripper.

Stepper motors with integrated encoder and lead screws have been adopted for the actuation of the end effector. This solution significantly simplifies the control and reduces the weight, the mechanical complexity and the cost of the end effector. Limit switches have been used for absolute position detection on both sides of all the end-effector movement axes. Each motor is driven by a Hydra servo drive control board, used as HW low-level motor controllers. These control boards are arranged on the end effector itself. The communication between the motor control boards and the high level WIRES controller is implemented through CAN bus. A ROS node has been developed to allow the control of the end effector and to ease the integration with other components of the WIRES system. At low level, the motors are controlled by means of the PLCOpen standard, allowing an easy implementation of the end effector controller. The tactile sensor has been integrated into the jaw tips (fingertips). Several versions of 3D printed fingers have been produced in order to evaluated different configurations during experiments.

### 3. Wire Shape Estimation

A specific sensor reference frame, Σs(Os
, xs

, ys), is defined at the center of the tactile sensor pad (see Figure 3) and the wire shape estimation problem is tackled with respect to this frame. The 16 taxels are organized as a matrix, where each cell can be identified by its row and column indices. Hence, for each cij cell it is possible to associate a couple of coordinates (xi

, yj), corresponding to the physical distances of the cell mechanical center from the sensor frame origin. In particular, the x-coordinates of the columns are −4.5 mm, −1.5 mm, 1.5 mm and 4.5 mm, from left to right, while the y-coordinates of the rows, are 4.5 mm, 1.5 mm, −1.5 mm and −4.5 mm, from top to bottom. The measured voltage variation corresponding to the cij cell is indicated as ∆vij.

xs

ys

Os

v11 | v12 | v13 | v14
v21 | v22 | v23 | v24
v32 | v33 | v34
v41 | v42 | v43 | v44

wire
edges

wire longitudinal axis

v31

Figure 3. Scheme of the grasped wire with respect to the sensor frame Σs and taxels.

In this paper, in order to estimate the shape of the grasped wire, this is locally approximated as a straight line, coincident with the longitudinal axis of the wire (see Figure 3), modelled in the Σs frame as the line with equation
ys = mxs + n, | (1)

where m and n are the two parameters to be identified by using the tactile data. Since the section of the grasped wire is considered a priori known, estimating the grasped wire shape means to estimate the m and n parameters characterizing longitudinal axis of the wire. The initial position of the wire implies that the grasped wire has the main direction always mainly aligned with the xs-axis (horizontal direction). In this hypothesis, the procedure for the wire shape estimation is constituted by a first step, where the centroid coordinates for each column are computed, and a second step, where the computation of the model parameters in (1) is implemented via a least squares method applied to the data set constituted by the coordinates of the column centroids. In detail,

step 1:

the y coordinates y

c
j

of the column centroids are computed from tactile data as

y

c
j =

∑

4
i=1

yi∆vij
∑

4
i=1 ∆vij
j = 1, . . . , 4, | (2)

where yi

is the mechanical y coordinate of the i-th row. Hence, the data set D¯ is constituted by the coordinates (xj
, y

c
j

) of the 4 column centroids (where xj is the mechanical x coordinate of the j-th column).

step 2:

the model (1) parameters, m, n, are estimated by using a least squares method applied to the data set D¯ resulting from step 1.
The presented procedure has been experimentally applied by grasping a wire in different configurations. Figure 4 reports a generic grasp: the tactile map shows how the cells on the second and the third rows present higher ∆vij values. The column centroids (green stars) have been computed by using Equation (2) and than the wire shape has been computed via least squares method (straight line). To assess the accuracy of the algorithm, a comparison among the estimated shapes and the actual ones has been carried out, superimposing a picture of the corresponding grasp to the measured data and estimated shapes. Figure 5 shows the good matching between the estimated and the actual wire shapes. The quality of the shape reconstruction is fundamental to successfully complete the insertion

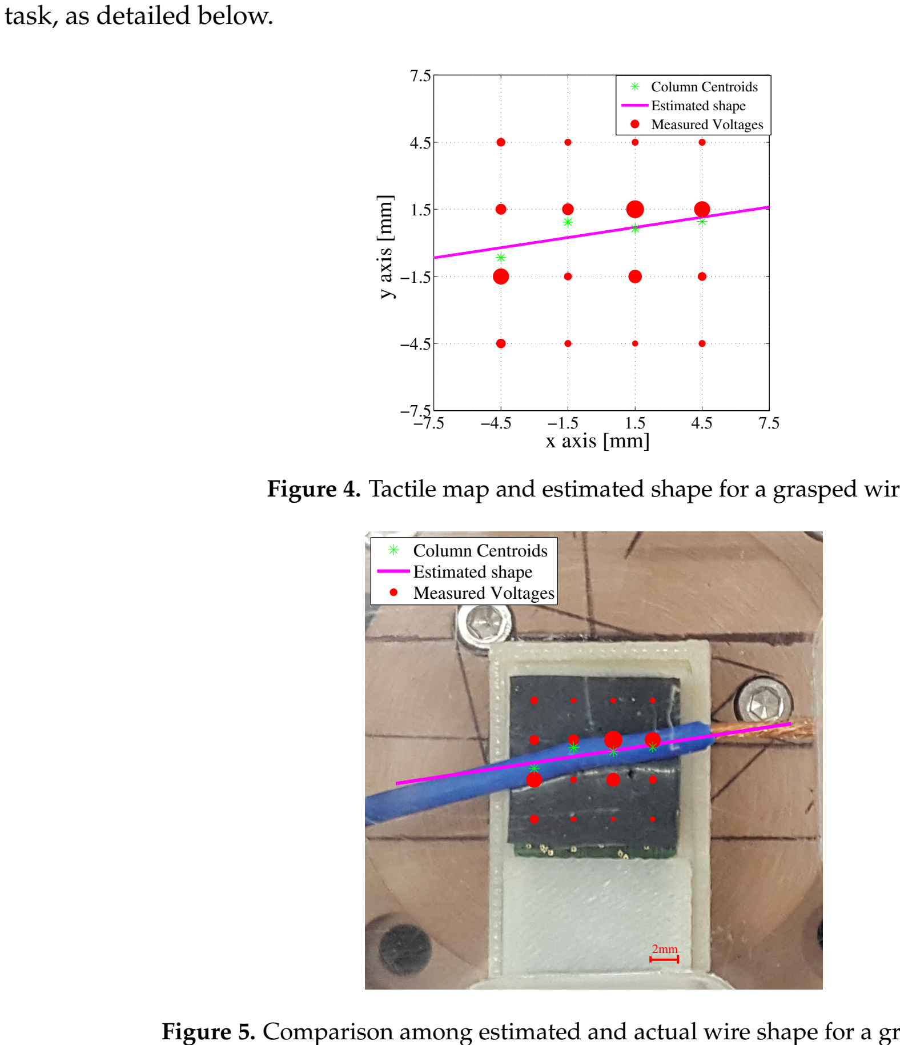
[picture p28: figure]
task, as detailed below.; x axis [mm]; y axis [mm]; Column Centroids Estimated shape Measured Voltages

Figure 4. Tactile map and estimated shape for a grasped wire.

2mm Figure 5. Comparison among estimated and actual wire shape for a grasped wire.

### 4. The Insertion Task

As discussed in Section 1, the main objective of the WIRES project is the robotic assembly of electric switchgears. To this aim, a fundamental subtask is represented by the insertion of the wire into the holes corresponding to the pins of the electrical components. The successful execution of the task allows the mechanical connection of the wire. The tactile sensor has been integrated into the gripper, suitably designed for the WIRES project in order to experimentally test its funcionalities during the insertion task. The proposed solution for the insertion task described in the following is based on the assumptions that the relative position between the robot system and the switchgear is known and, additionally, the length of the protruding part of the grasped wire is also known. Note that in real applications, a standard calibration procedure for the robot system allows us to obtain a precision that satisfies the first assumption. For the second assumption, the length of the protruding part of the wire can be estimated by using the camera integrated into the gripper as described in Section 2.
A human operator prepares the wire by placing it in a delimited area (based on the gripper stroke), with a random pose. The robotic system is used to grasp the wire and as a consequence, after grasping, the pose of the wire with respect to the tactile sensor is unknown. Then, the grasped wire shape is estimated by computing the model parameters m, n and applying the wire shape estimation algorithm. Figure 6a reports a sketch of a generic grasped wire, with the estimated shape. Let Σh
(Oh
, xh

, yh

) be
the hole frame, with the origin in the center of the hole and the xh
-axis aligned with the hole axis; let Σw(Ow, xw, yw) be the wire end frame, with the origin in the end point of the wire actual axis and the xw-axis aligned with the wire actual axis; let the frame Σˆ w(Oˆ w, xˆw, yˆw), with the origin in the end point of the estimated wire axis and the xˆw-axis aligned with the estimated wire axis. On the basis of the assumption described above, the poses of Σs and Σh are perfectly known, while the pose of Σˆ w can be computed from the estimated shape parameters m, n and the protruding part L value of the grasped wire. To this aim, the homogenous transformation matrix T

s
wˆ

can be computed from Figure 6a with simple geometrical considerations

T

s
wˆ =

cos γ | − sin γ | 0 | l cos γ
sin γ | cos γ | 0 l sin γ + n
0 | 0 | 1 | 0
0 | 0 | 0 | 1

, | (3)

where γ = arctan(m) and l = L + a/ cos γ (a is the half side length of the sensor pad). After the computation of Σˆ w, a standard technique can be used to program the robotic system in order to align Σˆ w with Σh

. After that, the resulting configuration is sketched in Figure 6b, with Σˆ w ≡Σh . From this
point the insertion task can be easily completed with a linear movement along the xh

-axis. In real
working conditions the hole diameter D is typically two times larger than the wire diameter d. Note that in this paper, the insertion has been tackled by considering the task a 2D problem; the z-axes are considered all aligned.

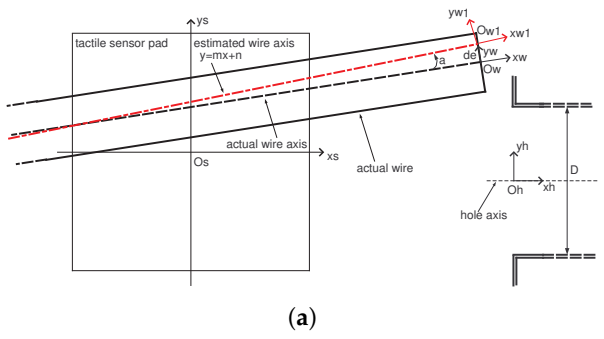
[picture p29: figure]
tactile sensor pad; estimated wire axis; actual wire; actual wire axis; hole axis

Figure 6. Cont.

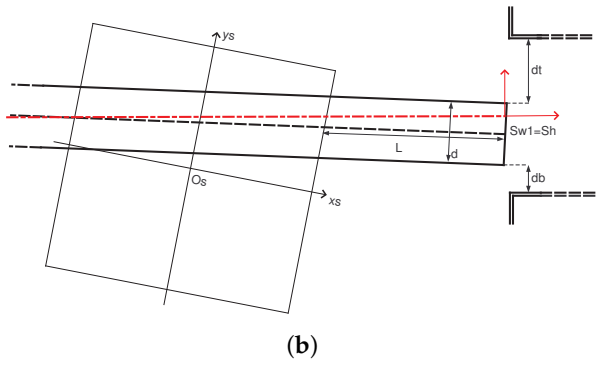
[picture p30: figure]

Figure 6. Sketch of the grasped wire with respect to the electric component before (a) and after (b) the alignment with the hole axis.

### 5. Assessment of Wire Shape Estimation and Expected Success Rate

In ideal conditions, when the estimation error of the wire shape is zero (i.e., Σˆ w ≡Σw), under the described assumptions, the proposed procedure allows us to align the wire axis and the hole axis, by maintaining the distances between wire and hole edges (both above δa and below δb

) equal to the
maximum possible value ¯δ = (D − d)/2. Obviously, in this case, the execution of the insertion task is guaranteed with a Success Rate SR = 100%. In real working conditions, the estimation error of the wire shape implies Σˆ w 6= Σw, and since the alignment can be made only between Σˆ w and Σh
, when the
estimation error increases the insertion task may fail. As a consequence, in real conditions the success rate of the insertion task is SR < 100%.
The quality of the estimated grasped wire shape and the maximum SR reachable can be evaluated taking into account both the estimation error and the actual diameters of the hole and the wire. In particular, the estimation error can be quantified by considering the relative poses of Σw and Σˆ w. The relative pose of these two frames can be represented by the following homogeneous transformation

T

wˆ
w =

cos α | − sin α | 0 −∆ sin α
sin α | cos α | 0 | ∆ cos α
0 | 0 | 1 | 0
0 | 0 | 0 | 1

, | (4)

where α is the angle between the estimated wire axis and the actual one, while ∆ is the distance between the origins of Σw and Σˆ w. In the ideal case, with a perfect shape estimation it is α = ∆ = 0 and T

wˆ

w = I. In real working conditions (α 6= 0, ∆ 6= 0), after the alignment Σˆ w ≡ Σh
(see Figure 6b),
the distances between wire and hole edges depends on ∆ and α. In particular, the estimation error implies that the actual position of the wire presents an offset along yh

-axis, which is responsible for any failure in the execution of the insertion task. This offset, computed from T

wˆ

w, is equal to ∆ cos α
and it reduces the space between wire and hole edges. The maximum limit for this offset, in order to avoid the unsuccessful execution of the task, is represented by the value ¯δ. As a consequence, the following metric
δ = ¯δ − ∆ cos α | (5)

can be computed to evaluate both the quality of the grasping and the expected result (success or not) of the insertion task execution. In conclusion, if 0 ≤ δ ≤ ¯δ the insertion can be successfully completed, while if δ < 0 the insertion task cannot be correctly completed. Moreover, the more δ is close to ¯δ, i.e., ∆ cos α → 0, the better is the quality of the estimated wire shape.

### 6. Experiments

A number of experiments have been carried out to evaluate the proposed approach. For each experiment, the wire shape has been computed according to the procedure detailed in Section 3. Tens of static experiments, with the sensor fixed on the workbench, have been used to evaluate the shape estimation quality and expected success rate. Additional experiments have been carried out to evaluate the actual success rate of the insertion task in real working conditions, by using the sensorized gripper with standard wires and electrical component.

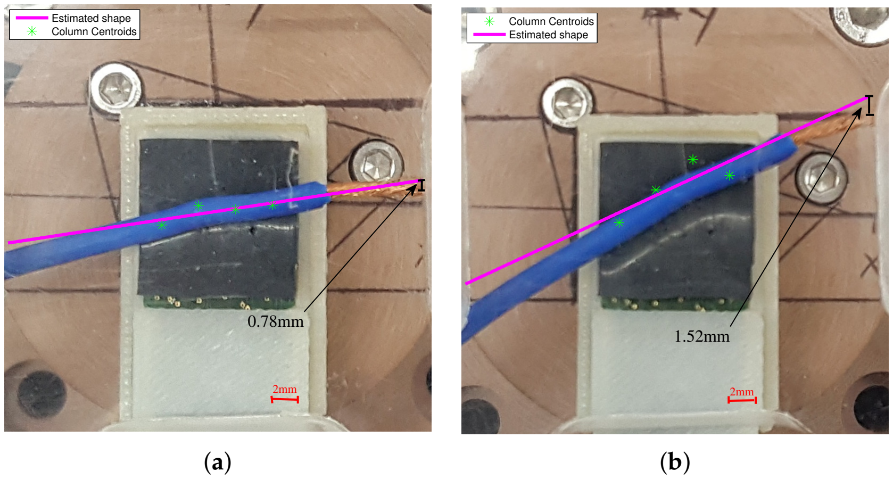
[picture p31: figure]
Estimated shape Column Centroids; Column Centroids Estimated shape

Figure 7. Some pictures of grasped wires with the estimated shapes and the offset errors ∆ cos α:
(a) reports a standard case, while (b) reports a borderline case.
6.1. Estimation Quality and Expected SR

For the first set of experiments, a standard wire with d = 3 mm has been grasped between the tactile sensor, fixed on the workbench, and a transparent methacrylate plate, in different poses. By considering the diameter of the hole of the electric component D = 2d, it is ¯δ = 1.5 mm. A calibrated optical microscope has been used to take pictures from the transparent plate side. Hence, the offset errors ∆ cos α between the estimated and the actual wire end points can be directly measured from the pictures. Figure 7 reports two sample cases, where the estimated wire shapes are compared to the actual ones. For each considered case the value of the offset error is reported. By using Equation (5) the metric can be computed, obtaining for the cases in Figure 7 the following values: δ = 0.72 mm for case (a) and δ = −0.02 mm for case (b). From these values it is evident that case (a) allows the correct execution of the insertion task, while case (b) does not guarantee a correct insertion phase (δ < 0). Note that case (b) corresponds to a grasp configuration close to the diagonal of the sensor pad (that is quite unlikely). The same procedure has been applied to 20 considered experiments. Finally, all grasping cases have been divided into two sets: the first set corresponding to cases with a computed metric δ > 0 (17 experiments) and a second set with δ < 0 (3 experiments). The expected success rate for the insertion task has been computed, by relating the number of experiments within the first set with respect to the total number of experiments, by obtaining a SR = 85%.

6.2. The Insertion Task Implementation

For the implementation of the insertion task, the sensorized gripper has been used. All measurements are reported with respect to the world reference frame Σ(O, x, y), placed at the robot base. Position and orientation of Σs with respect to Σ is known in each time instant, by using the robot system kinematics. The pose of the electric component hole is defined by Σh
, assumed known from the
switchgear CAD. Figure 8 reports experimental results for the s pose during an insertion task. After the wire grasping, the xs-axis is aligned to the xh

-axis during an approaching phase (see Figure 8a), leaving a distance between Os and Oh equal to 22 mm in this specific case (it is the estimated length L plus the half side length a of the sensor pad). The reached configuration (at t = 10 s) is reported in Figure 9a, where the estimated wire shape and the frame poses (Σs

, Σˆ w, Σh
) are reported with
respect to Σ, together with the tactile sensor pad and the component hole. It is evident that without a correction the insertion cannot be completed correctly. The wire shape has been estimated by applying the wire shape estimation algorithm, and the parameters m and n have been used to compute the homogeneous transformation (3). For the experiment reported in the figures m = −0.0694 and n = −3.4866. By using the computed homogeneous transformation, Σˆ w has been aligned with Σh during the correction phase. Figure 8b shows a zoom of the rotation and the translation applied during the correction. After this phase, the estimated wire axis is aligned with the component hole axis. The reached configuration (at t = 22 s) is reported in Figure 9b, where it is evident that the insertion can now be correctly completed with a simple translation along the x-axis. Figure 8a shows also the final insertion phase. Figure 10 reports the flowchart, where the connections among all subtasks of the whole insertion sequence are reported. Several checks are implemented by using the tactile sensor data during the insertion execution, in order to evaluate if the task is correctly completed or not. During experiments, the wire shape estimation error will affect the final success of the insertion phase. As discussed in Section 5, the actual wire end point is related to the Σw frame, while the estimated wire end point is identified by the Σˆ w frame. To test how this estimation error affects the insertion phase during experiments in real working conditions, the insertion task has been repeated 40 times starting from different initial grasping conditions for the wire. The same experiment described above has been executed and, for each case, the final correct insertion has been evaluated. The number of successfully completed tasks was 33 with a success rate SR = 82.5%. The obtained SR is slightly below the expected SR computed in static conditions (see Section 5), as was foreseeable, since during the experiments, additional errors (e.g., robotic system calibration, electric component position) appears together with the wire shape estimation error. Figure 11 reports a sequence of frames extracted from the video (https://youtu.be/oPxkeeQLKi8) related to the paper in order to show how the designed gripper with the proposed approach allow to correctly complete an insertion sequence. Each frame has been marked with the corresponding procedure subtask. The video shows the effectiveness of the proposed approach during a demo. In the video, the robot is used to fix the screwdriver position for the connection, while the insertion is completely implemented by the designed gripper.

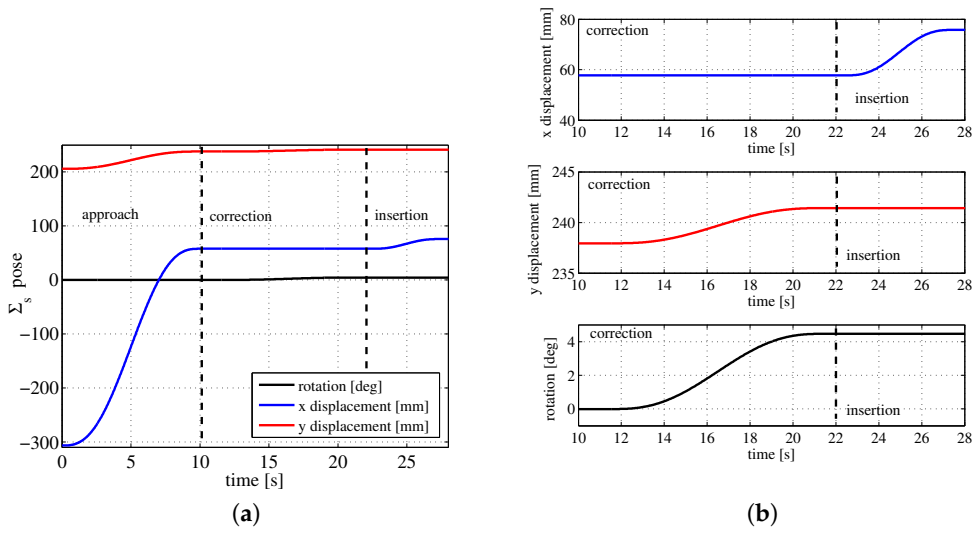
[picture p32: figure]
time [s]; s pose; rotation [deg]; approach; correction; insertion; x displacement [mm]; y displacement [mm]

x displacement [mm] y displacement [mm]

Figure 8. Experimental results: (a) Σs pose during the whole insertion subtask and (b) zoom of the correction and insertion phases.

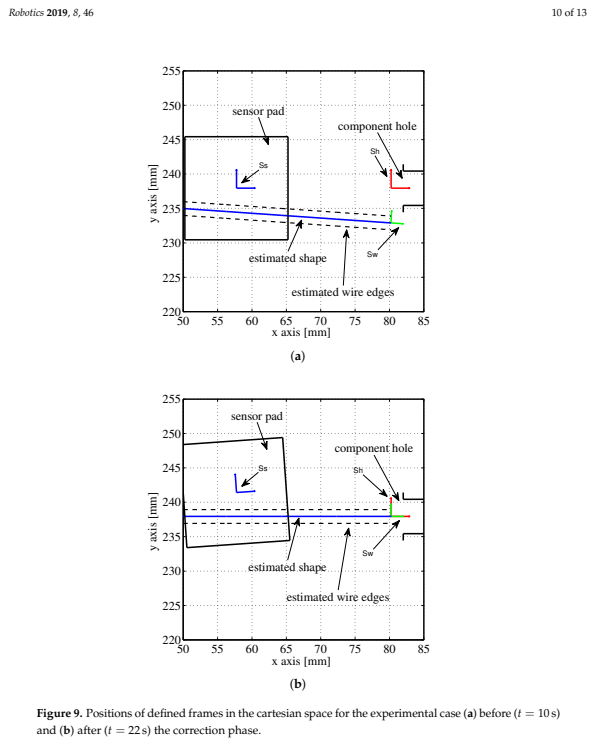
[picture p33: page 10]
x axis [mm]; y axis [mm]

sensor pad | | component hole

estimated shape | | Sw

estimated wire edges

sensor pad

Ss | component hole

estimated shape | | Sh (b) Sw

Figure 9. Positions of defined frames in the cartesian space for the experimental case (a) before (t = 10 s)
and (b) after (t = 22 s) the correction phase.

Start

Move robot to home position and open gripper

Move robot to initial position for the next wire

Close gripper to grasp the wire

Check the grasping by
using tactile data

Move robot and gripper to the nominal pre-insertion position

Move robot to place the screwdriver on the screw

Correction: compute the wire model parameters and move gripper to the corrected pre-insertion position

Insertion: move forward the gripper of a fixed displacement

Screwing: activate the screwdriver and move the robot to complete the screwing

OK

OK

OK

NOT OK

NOT OK

NOT OK

Mark the wire as correctly connected

Mark the wire as
not connected

Check the insertion
by using tactile data

Check the screwing
by using tactile data

Move backward the gripper of a fixed diplacement

Figure 10. Flowchart of the whole insertion sequence.

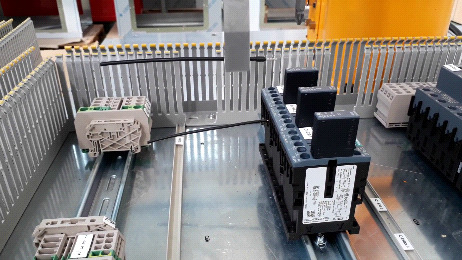
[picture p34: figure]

Approach to nominal
pre-insertion position

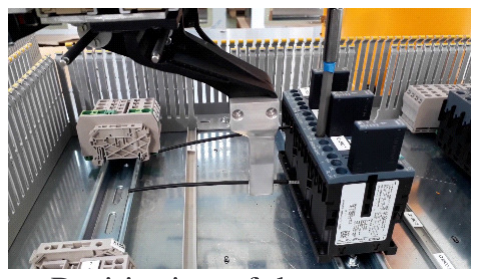
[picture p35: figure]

Positioning of the
screwdriver on the screw

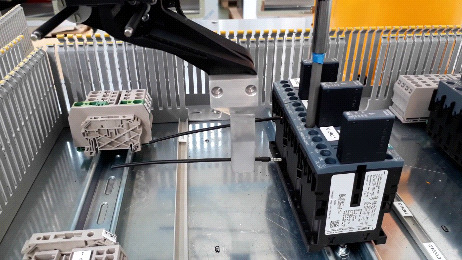
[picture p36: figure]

Computation of
model parameters

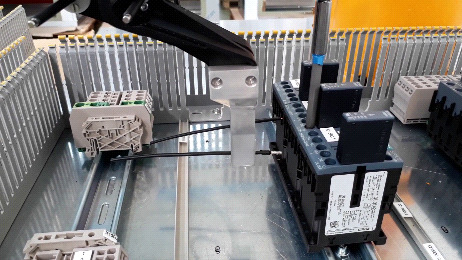
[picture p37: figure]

Correction of the

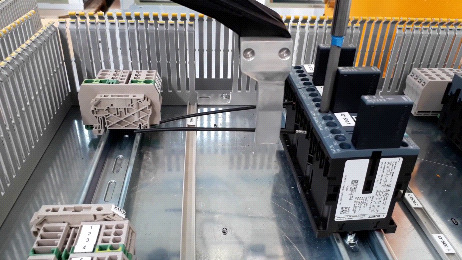
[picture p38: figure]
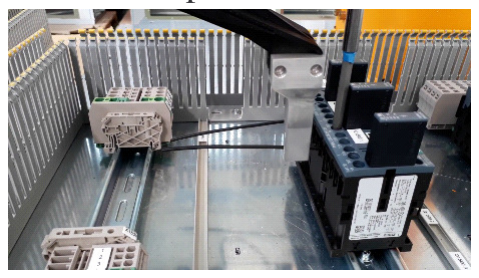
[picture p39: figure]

pre-insertion position | Insertion | Screwing

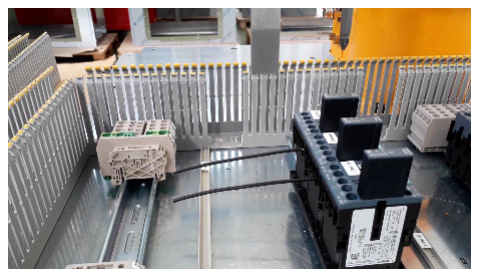
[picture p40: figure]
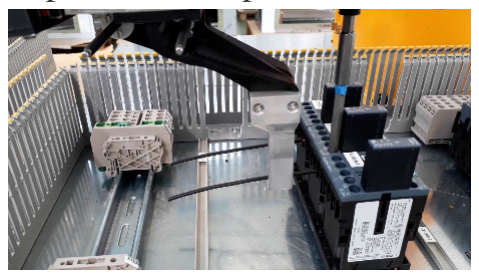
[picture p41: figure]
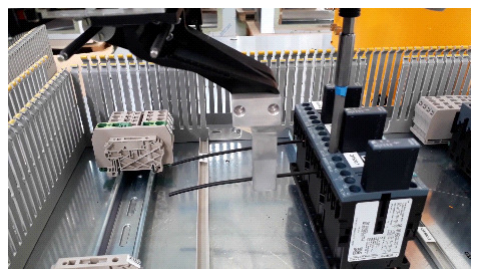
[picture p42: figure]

Move backward the gripper | Screwing check | Move to next wire

Figure 11. Sequence of frames during some detailed phases of an insertion task.

### 7. Conclusions

This paper presented a sensorized gripper for wire manipulation, and in particular, for their insertion into the electric components of a switchgear. The designed gripper integrates tactile sensors suitably optimized for this task. A specific procedure for the insertion task execution has been proposed and evaluated in terms of expected success rate. Experimental results have been reported to show the effectiveness of the proposed strategy. Future work will pprobably be devoted to using the sensor to estimate contact forces between the gripper and the manipulated wire during the whole assembly process of the switchgear.

Supplementary Materials: The following are available online at http://www.mdpi.com/2218-6581/8/2/46/s1.

Author Contributions: Design and development of the end-effector, G.P.; Design and development of the tactile sensor, S.P.; Integration, methodology and experimental validation, G.P. and S.P.

Funding: This work was supported by the European Commission’s Seventh Framework Programme (FP7/2007-20013) under Grant agreement NO. 601116 (ECHORD++—WIRES Experiment).

Conflicts of Interest: The authors declare no conflict of interest. The founding sponsors had no role in the design of the study; in the collection, analyses, or interpretation of data; in the writing of the manuscript, and in the decision to publish the results.

References

1. Busi, M.; Cirillo, A.; De Gregorio, D.; Indovini, M.; De Maria, G.; Melchiorri, C.; Natale, C.; Palli, G.; Pirozzi, S. The WIRES Experiment: Tools and Strategies for Robotized Switchgear Cabling. Procedia Manuf. 2017, 11, 355–363. [CrossRef] (http://dx.doi.org/10.1016/j.promfg.2017.07.118)
2. Cirillo, A.; De Maria, G.; Natale, C.; Pirozzi, S. Design and Evaluation of Tactile Sensors for the Estimation of Grasped Wire Shape. In Proceedings of the IEEE International Conference on Advanced Intelligent Mechatronics, Munich, Germany, 3–7 July 2017; pp. 490–496.

3. De Gregorio, D.; Zanella, R.; Palli, G.; Pirozzi, S.; Melchiorri, C. Integration of Robotic Vision and Tactile Sensing for Wire-Terminal Insertion Tasks. IEEE Trans. Autom. Sci. Eng. 2018, in press. [CrossRef] (http://dx.doi.org/10.1109/TASE.2018.2847222)
4. Saxena, A.; Driemeyer, J.; Ng, A.Y. Robotic Grasping of Novel Objects using Vision. Int. J. Robot. Res. 2008, 27, 157–173. [CrossRef] (http://dx.doi.org/10.1177/0278364907087172)
5. Allen, P.K. Integrating Vision and Touch for Object Recognition Tasks. Int. J. Robot. Res. 1988, 7, 15–33. [CrossRef] (http://dx.doi.org/10.1177/027836498800700603)
6. Björkman, M.; Bekiroglu, Y.; Högman, V.; Kragic, D. Enhancing visual perception of shape through tactile glances. In Proceedings of the IEEE/RSJ International Conference on Intelligent Robots and Systems, Tokyo, Japan, 3–7 November 2013; pp. 3180–3186.
7. Bimbo, J.; Seneviratne, L.D.; Althoefer, K.; Liu, H. Combining touch and vision for the estimation of an object’s pose during manipulation. In Proceedings of the International Conference on Intelligent Robots and Systems, Tokyo, Japan, 3–7 November 2013; pp. 4021–4026.
8. Bhattacharjee, T.; Shenoi, A.A.; Park, D.; Rehg, J.M.; Kemp, C.C. Combining tactile sensing and vision for rapid haptic mapping. In Proceedings of the International Conference on Intelligent Robots and Systems, Hamburg, Germany, 28 September–2 October 2015; pp. 1200–1207.
9. Lepora, N.F.; Aquilina, K.; Cramphorn, L. Exploratory Tactile Servoing With Active Touch. IEEE Robot. Autom. Lett. 2017, 2, 1156–1163. [CrossRef] (http://dx.doi.org/10.1109/LRA.2017.2662071)
10. Aggarwal, A.; Kirchner, F. Object Recognition and Localization: The Role of Tactile Sensors. Sensors 2014, 14, 3227–3266. [CrossRef] (http://dx.doi.org/10.3390/s140203227) [PubMed] (http://www.ncbi.nlm.nih.gov/pubmed/24553087)
11. Yamaguchi, A.; Atkeson, C.G. Combining finger vision and optical tactile sensing: Reducing and handling errors while cutting vegetables. In Proceedings of the 2016 IEEE-RAS 16th International Conference on Humanoid Robots (Humanoids), Cancun, Mexico, 15–17 November 2016; pp. 1045–1051.
12. Pirozzi, S.; Natale, C. Tactile-based manipulation of wires for switchgear assembly. IEEE/ASME Trans. Mechatron. 2018, 23, 2650–2661. [CrossRef] (http://dx.doi.org/10.1109/TMECH.2018.2869477)

c 2019 by the authors. Licensee MDPI, Basel, Switzerland. This article is an open access article distributed under the terms and conditions of the Creative Commons Attribution (CC BY) license (http://creativecommons.org/licenses/by/4.0/).

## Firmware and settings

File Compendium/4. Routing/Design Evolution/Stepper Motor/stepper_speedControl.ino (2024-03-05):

/*Example sketch to control a stepper motor with A4988/DRV8825 stepper motor driver and Arduino without a library. More info: https://www.makerguides.com */

// Define stepper motor connections and steps per revolution:
#define dirPin 2
#define stepPin 3
#define stepsPerRevolution 200

void setup() {
  // Declare pins as output:
  pinMode(stepPin, OUTPUT);
  pinMode(dirPin, OUTPUT);
}

void loop() {
  // Set the spinning direction clockwise:
  digitalWrite(dirPin, HIGH);

  // Spin the stepper motor 1 revolution slowly:
  for (int i = 0; i < stepsPerRevolution; i++) {
    // These four lines result in 1 step:
    digitalWrite(stepPin, HIGH);
    delayMicroseconds(2000);
    digitalWrite(stepPin, LOW);
    delayMicroseconds(2000);
  }

//  delay(1000);

//  // Set the spinning direction counterclockwise:
//  digitalWrite(dirPin, LOW);
//
//  // Spin the stepper motor 1 revolution quickly:
//  for (int i = 0; i < stepsPerRevolution; i++) {
//    // These four lines result in 1 step:
//    digitalWrite(stepPin, HIGH);
//    delayMicroseconds(1000);
//    digitalWrite(stepPin, LOW);
//    delayMicroseconds(1000);
//  }
//
//  delay(1000);

//  // Set the spinning direction clockwise:
//  digitalWrite(dirPin, HIGH);
//
//  // Spin the stepper motor 5 revolutions fast:
//  for (int i = 0; i < 5 * stepsPerRevolution; i++) {
//    // These four lines result in 1 step:
//    digitalWrite(stepPin, HIGH);
//    delayMicroseconds(500);
//    digitalWrite(stepPin, LOW);
//    delayMicroseconds(500);
//  }
//
//  delay(1000);
//
//  // Set the spinning direction counterclockwise:
//  digitalWrite(dirPin, LOW);
//
//  //Spin the stepper motor 5 revolutions fast:
//  for (int i = 0; i < 5 * stepsPerRevolution; i++) {
//    // These four lines result in 1 step:
//    digitalWrite(stepPin, HIGH);
//    delayMicroseconds(350);
//    digitalWrite(stepPin, LOW);
//    delayMicroseconds(350);
//  }
//
//  delay(1000);
}
